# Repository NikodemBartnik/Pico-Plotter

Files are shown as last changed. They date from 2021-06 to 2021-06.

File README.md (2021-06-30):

# Pico Plotter
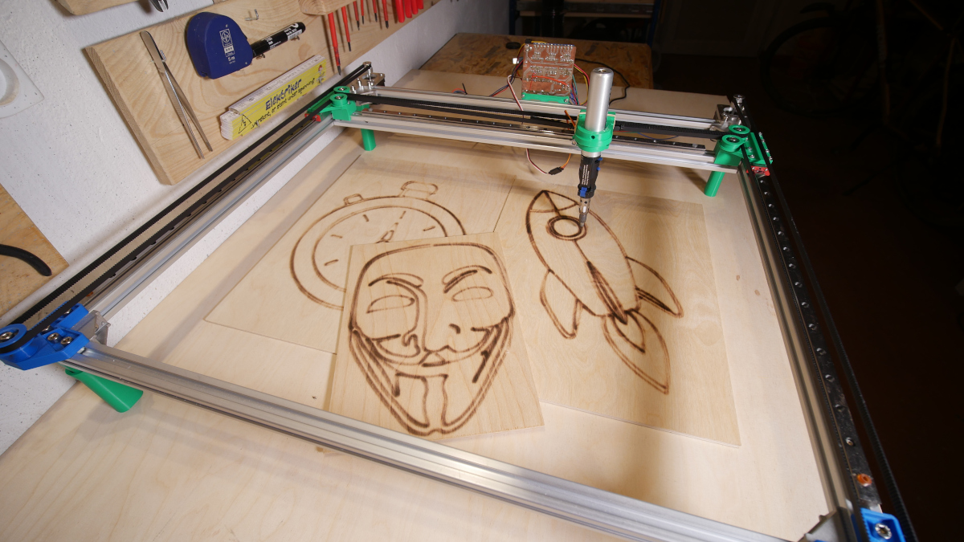
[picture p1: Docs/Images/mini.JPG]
Pico Plotter image

3D printed Raspberry Pi Pico H-Bot plotter programmed in MicroPython capable of drawing on paper and burning wood with versatip.

## Description

Main purpose of this project was to practice Python programing, design something cool and understand basics of how CNC machines, Gcode senders etc. works. This project is probably a great starting point to learn about basics of any CNC machine, as it is very simple and code is very minimal. 3D printed parts are optimized for support less printing (most of them but not all) and can be printed out of PLA. 
## Parts
#### Electronics
| Name | Amount | Link 1 | Link 2 | Link 3 |
| --- | --- | --- | --- | --- |
| Motors | 2 | [https://bit.ly/3jrCJqY](https://bit.ly/3jrCJqY) | [https://bit.ly/3w9vsim](https://bit.ly/3w9vsim) | [https://amzn.to/3jlCU7o](https://amzn.to/3jlCU7o) |
| Stepper drivers | 2 | [https://bit.ly/3608XSl](https://bit.ly/3608XSl) | [https://bit.ly/3Abaz9P](https://bit.ly/3Abaz9P) | [https://amzn.to/3yjyXV9](https://amzn.to/3yjyXV9) |
| Power supply | 1 | [https://bit.ly/3qzeEjz](https://bit.ly/3qzeEjz) | [https://bit.ly/3qzJbxF](https://bit.ly/3qzJbxF) | [https://amzn.to/2T9NVOx](https://amzn.to/2T9NVOx) |
| Raspberry Pi Pico | 1 | [https://bit.ly/2US6Spl](https://bit.ly/2US6Spl) | [https://bit.ly/3Aegafp](https://bit.ly/3Aegafp) | [https://amzn.to/2Tjz9Vd](https://amzn.to/2Tjz9Vd) |
| USB to UART converter | 1 | [https://bit.ly/3vZQIqF](https://bit.ly/3vZQIqF) | [https://bit.ly/36488Il](https://bit.ly/36488Il) | [https://amzn.to/3dsafcT](https://amzn.to/3dsafcT) |
| Micro servo | 1 | [https://bit.ly/3A8MjoF](https://bit.ly/3A8MjoF) | [https://bit.ly/3jrOihS](https://bit.ly/3jrOihS) | [https://amzn.to/367zPQh](https://amzn.to/367zPQh) |
| Small components | \- | | |
#### Mechanics
| Name | Amount | Link 1 | Link 2 | Link 3 |
| --- | --- | --- | --- | --- |
| Aluminium profile 2020 600mm | 5 | [https://bit.ly/2UF2auT](https://bit.ly/2UF2auT) | [https://bit.ly/3hjPS2F](https://bit.ly/3hjPS2F) | [https://amzn.to/2UcRjs5](https://amzn.to/2UcRjs5) |
| MGN12 Linear rail 500mm | 3 | [https://bit.ly/3qwWoHM](https://bit.ly/3qwWoHM) | [https://bit.ly/3jvdd4f](https://bit.ly/3jvdd4f) | [https://amzn.to/3Adcs5K](https://amzn.to/3Adcs5K) |
| MGN12H linear block | 5 | [https://bit.ly/3qyKxsE](https://bit.ly/3qyKxsE) | [https://bit.ly/3AkVN0r](https://bit.ly/3AkVN0r) | [https://amzn.to/3h266yv](https://amzn.to/3h266yv) |
| GT2 Pulley | 2 | [https://bit.ly/3y7doGW](https://bit.ly/3y7doGW) | [https://bit.ly/3AbJDXp](https://bit.ly/3AbJDXp) | [https://amzn.to/3h2xc8I](https://amzn.to/3h2xc8I) |
| GT2 Belt | 5m | [https://bit.ly/3h44CUH](https://bit.ly/3h44CUH) | [https://bit.ly/2U5sbDr](https://bit.ly/2U5sbDr) | [https://amzn.to/3x8Wgk0](https://amzn.to/3x8Wgk0) |
| 625ZZ Bearing | 6 | [https://bit.ly/2USf3Sz](https://bit.ly/2USf3Sz) | [https://bit.ly/2TbLKKo](https://bit.ly/2TbLKKo) | [https://amzn.to/3vZVZyt](https://amzn.to/3vZVZyt) |
| Corner connectors | 4 | [https://bit.ly/3h1PA1G](https://bit.ly/3h1PA1G) | [https://bit.ly/3qLDTj3](https://bit.ly/3qLDTj3) | [https://amzn.to/2Ua83Af](https://amzn.to/2Ua83Af) |
| Screws, T nuts etc. | | | |
#### Tools
| Name | Link 1 | Link 2 | Link 3 |
| --- | --- | --- | --- |
| 3D printer | [https://bit.ly/3qxoAu7](https://bit.ly/3qxoAu7) | [https://bit.ly/3xZZaHU](https://bit.ly/3xZZaHU) | [https://amzn.to/3y25gHV](https://amzn.to/3y25gHV) |
| CNC Machine | [https://indystry.cc/indymill/](https://indystry.cc/indymill/) | [https://indystry.cc/dremel-cnc/](https://indystry.cc/dremel-cnc/) | |
| Gas soldering iron | [https://amzn.to/3jEaGoH](https://amzn.to/3jEaGoH) | [https://bit.ly/3dqgHBm](https://bit.ly/3dqgHBm) |
## Getting Started
You don't need any special libraries or additional files, assuming you have Python installed you have everything you need.
In order to upload script to Raspberry Pi Pico I used [Thonny](https://thonny.org/)

### Executing program
Before executing the Gcode sender change port of your raspberry pi pico and also path to the file that you want to print
To execute Gcode sender script simply change directory to where the file is located and type in the terminal:
```
python GcodeSender.py
```

## Help

If you need help, see the problem or want to contribute open an issue.

## Author
[Nikodem Bartnik](https://nikodembartnik.pl/)

## License

This project is licensed under the MIT license.

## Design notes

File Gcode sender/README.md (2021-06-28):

Very simple command line based Gcode sender. Not really useful for bigger projects, but great to understand how such things work, experiment and control the Pico Plotter.

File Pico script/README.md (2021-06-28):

MicroPython script for Raspberry Pi Pico for a pico plotter

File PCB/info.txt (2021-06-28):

Here are links to libraries I used for this PCB:
https://github.com/Lobo-T/RPI-Pico-Eagle-lib

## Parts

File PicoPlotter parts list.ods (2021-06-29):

Electronics
Name | Amount | Link 1 | Link 2 | Link 3 | Comments
Motors | 2 | https://bit.ly/3jrCJqY | https://bit.ly/3w9vsim | https://amzn.to/3jlCU7o
Stepper drivers | 2 | https://bit.ly/3608XSl | https://bit.ly/3Abaz9P | https://amzn.to/3yjyXV9
Power supply | 1 | https://bit.ly/3qzeEjz | https://bit.ly/3qzJbxF | https://amzn.to/2T9NVOx | 12V 3A
Raspberry Pi Pico | 1 | https://bit.ly/2US6Spl | https://bit.ly/3Aegafp | https://amzn.to/2Tjz9Vd
USB to UART converter | 1 | https://bit.ly/3vZQIqF | https://bit.ly/36488Il | https://amzn.to/3dsafcT
Micro servo | 1 | https://bit.ly/3A8MjoF | https://bit.ly/3jrOihS | https://amzn.to/367zPQh
Small components | - |  |  |  | Pin headers, LEDs
Mechanics
Name | Amount | Link 1 | Link 2 | Link 3 | Comments
Aluminium profile 2020 600mm | 5 | https://bit.ly/2UF2auT | https://bit.ly/3hjPS2F | https://amzn.to/2UcRjs5
MGN12 Linear rail 500mm | 3 | https://bit.ly/3qwWoHM | https://bit.ly/3jvdd4f | https://amzn.to/3Adcs5K | Usually one liner block is included in each rail so you may need to buy only 2 additional blocks
MGN12H linear block | 5 | https://bit.ly/3qyKxsE | https://bit.ly/3AkVN0r | https://amzn.to/3h266yv
GT2 Pulley | 2 | https://bit.ly/3y7doGW | https://bit.ly/3AbJDXp | https://amzn.to/3h2xc8I
GT2 Belt | 5m | https://bit.ly/3h44CUH | https://bit.ly/2U5sbDr | https://amzn.to/3x8Wgk0
625ZZ Bearing | 6 | https://bit.ly/2USf3Sz | https://bit.ly/2TbLKKo | https://amzn.to/3vZVZyt
Corner connectors | 4 | https://bit.ly/3h1PA1G | https://bit.ly/3qLDTj3 | https://amzn.to/2Ua83Af
Screws, T nuts etc.
Tools
Name | Amount | Link 1 | Link 2 | Link 3 | Comments
3D printer |  | https://bit.ly/3qxoAu7 | https://bit.ly/3xZZaHU | https://amzn.to/3y25gHV
CNC Machine |  | https://indystry.cc/indymill/ | https://indystry.cc/dremel-cnc/
Gas soldering iron |  | https://amzn.to/3jEaGoH | https://bit.ly/3dqgHBm |  | I am using the versatip from Dremel, never tested the other one

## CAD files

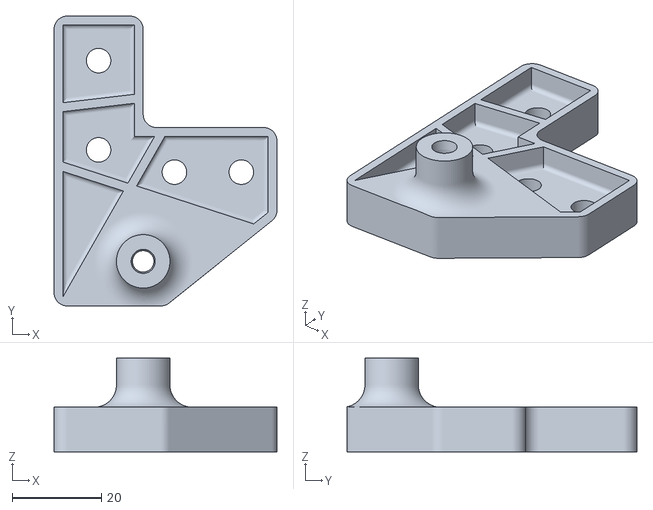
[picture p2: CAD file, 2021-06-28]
3D printed/Bearing holder left.stl
50.0 x 65.0 x 21.0

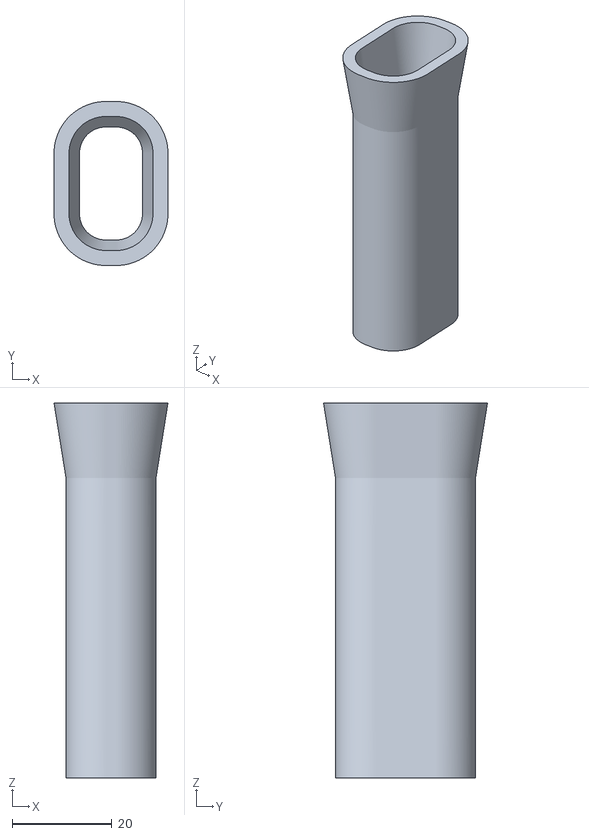
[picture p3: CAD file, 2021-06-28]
3D printed/Leg extension.stl
22.8 x 32.8 x 75.0

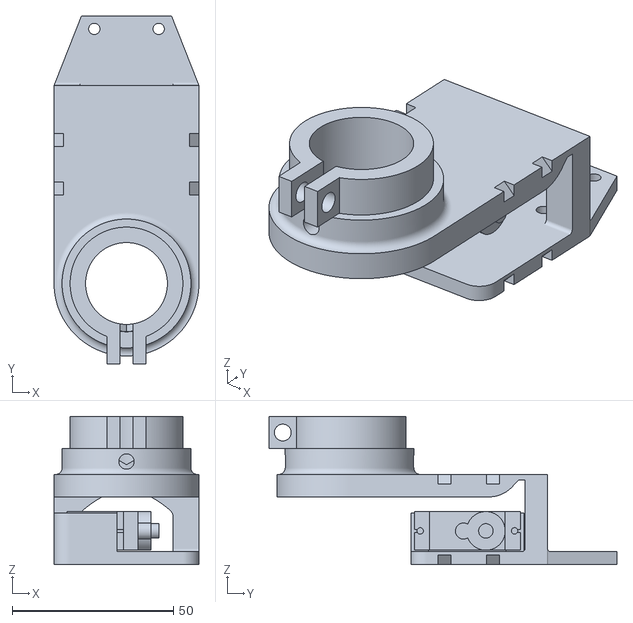
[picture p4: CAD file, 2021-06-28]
3D printed/X carriage.stl
45.0 x 108.1 x 46.0

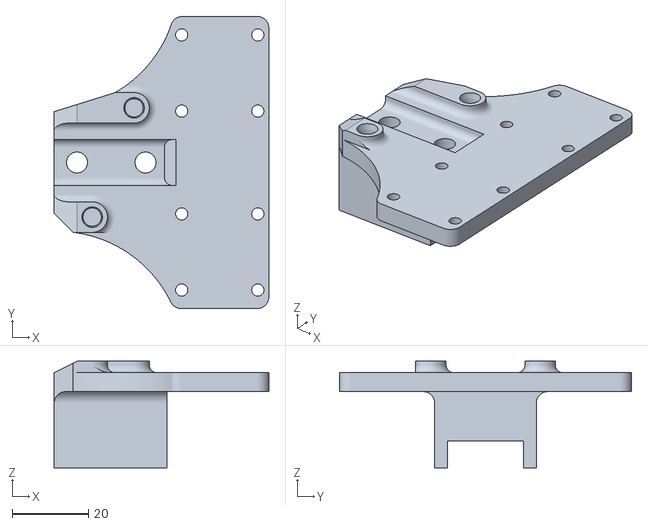
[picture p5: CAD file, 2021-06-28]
3D printed/Y right.stl
56.4 x 76.7 x 28.0

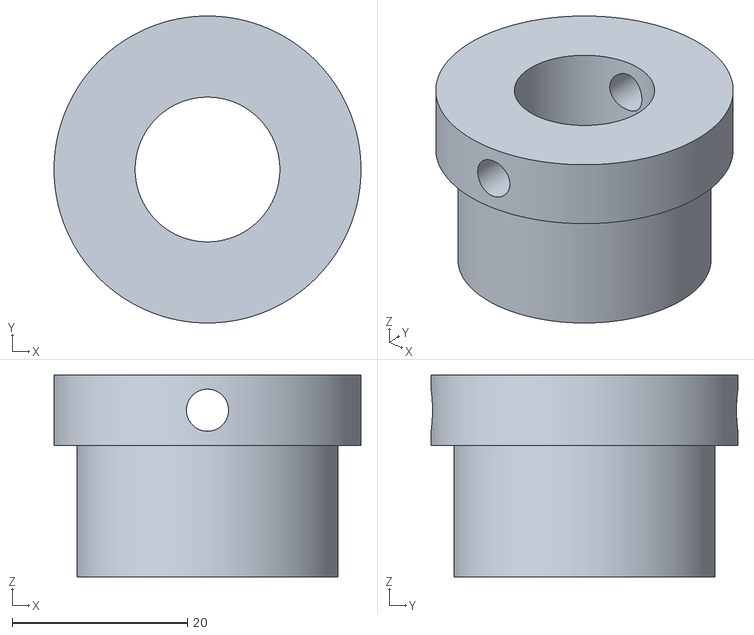
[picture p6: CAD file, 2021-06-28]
3D printed/Pen holder.stl
35.0 x 35.0 x 23.0

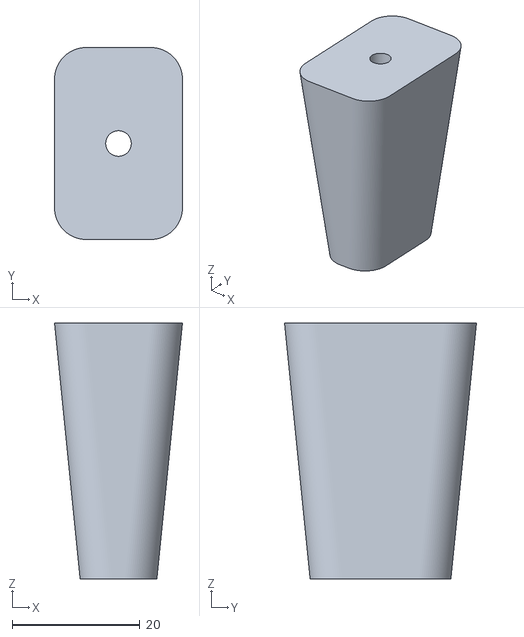
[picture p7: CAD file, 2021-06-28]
3D printed/Leg.stl
20.0 x 30.0 x 40.0

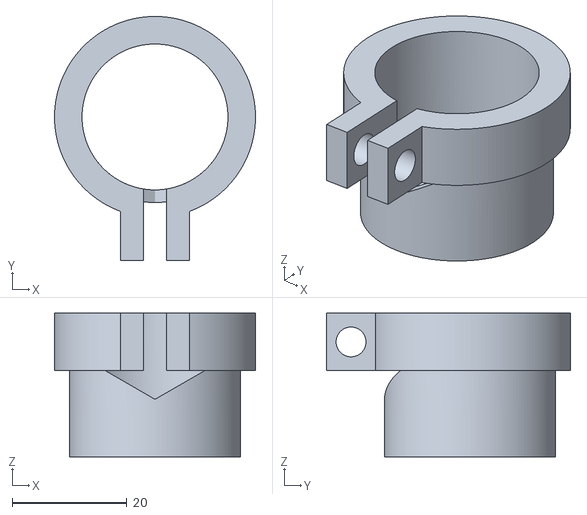
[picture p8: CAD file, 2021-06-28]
3D printed/Verastip holder.stl
35.0 x 42.5 x 25.0

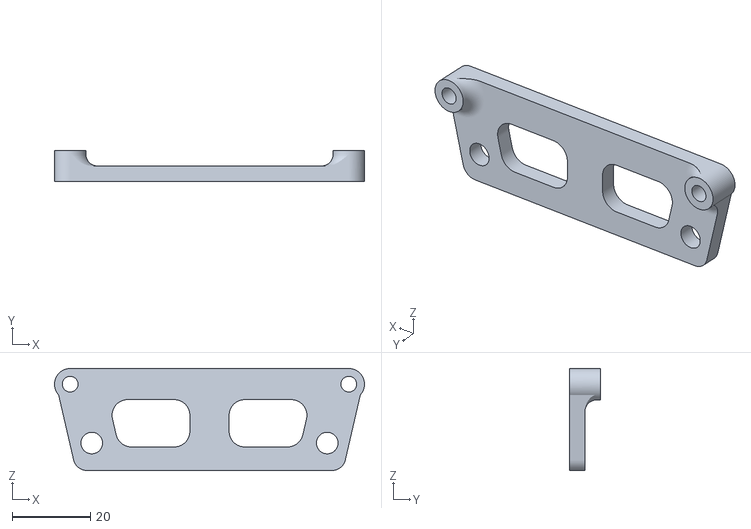
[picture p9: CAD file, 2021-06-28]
3D printed/PCB holder.stl
79.0 x 8.00 x 26.0

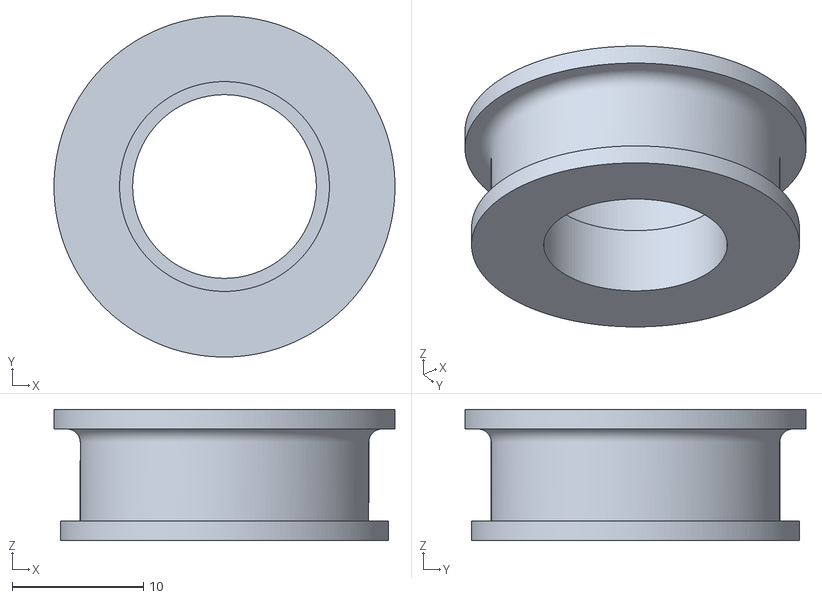
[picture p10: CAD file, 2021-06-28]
3D printed/pulley.stl
26.0 x 26.0 x 10.0

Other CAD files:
3D printed/Bearing holder right.stl
3D printed/Y left.stl
PicoPlotter.f3z

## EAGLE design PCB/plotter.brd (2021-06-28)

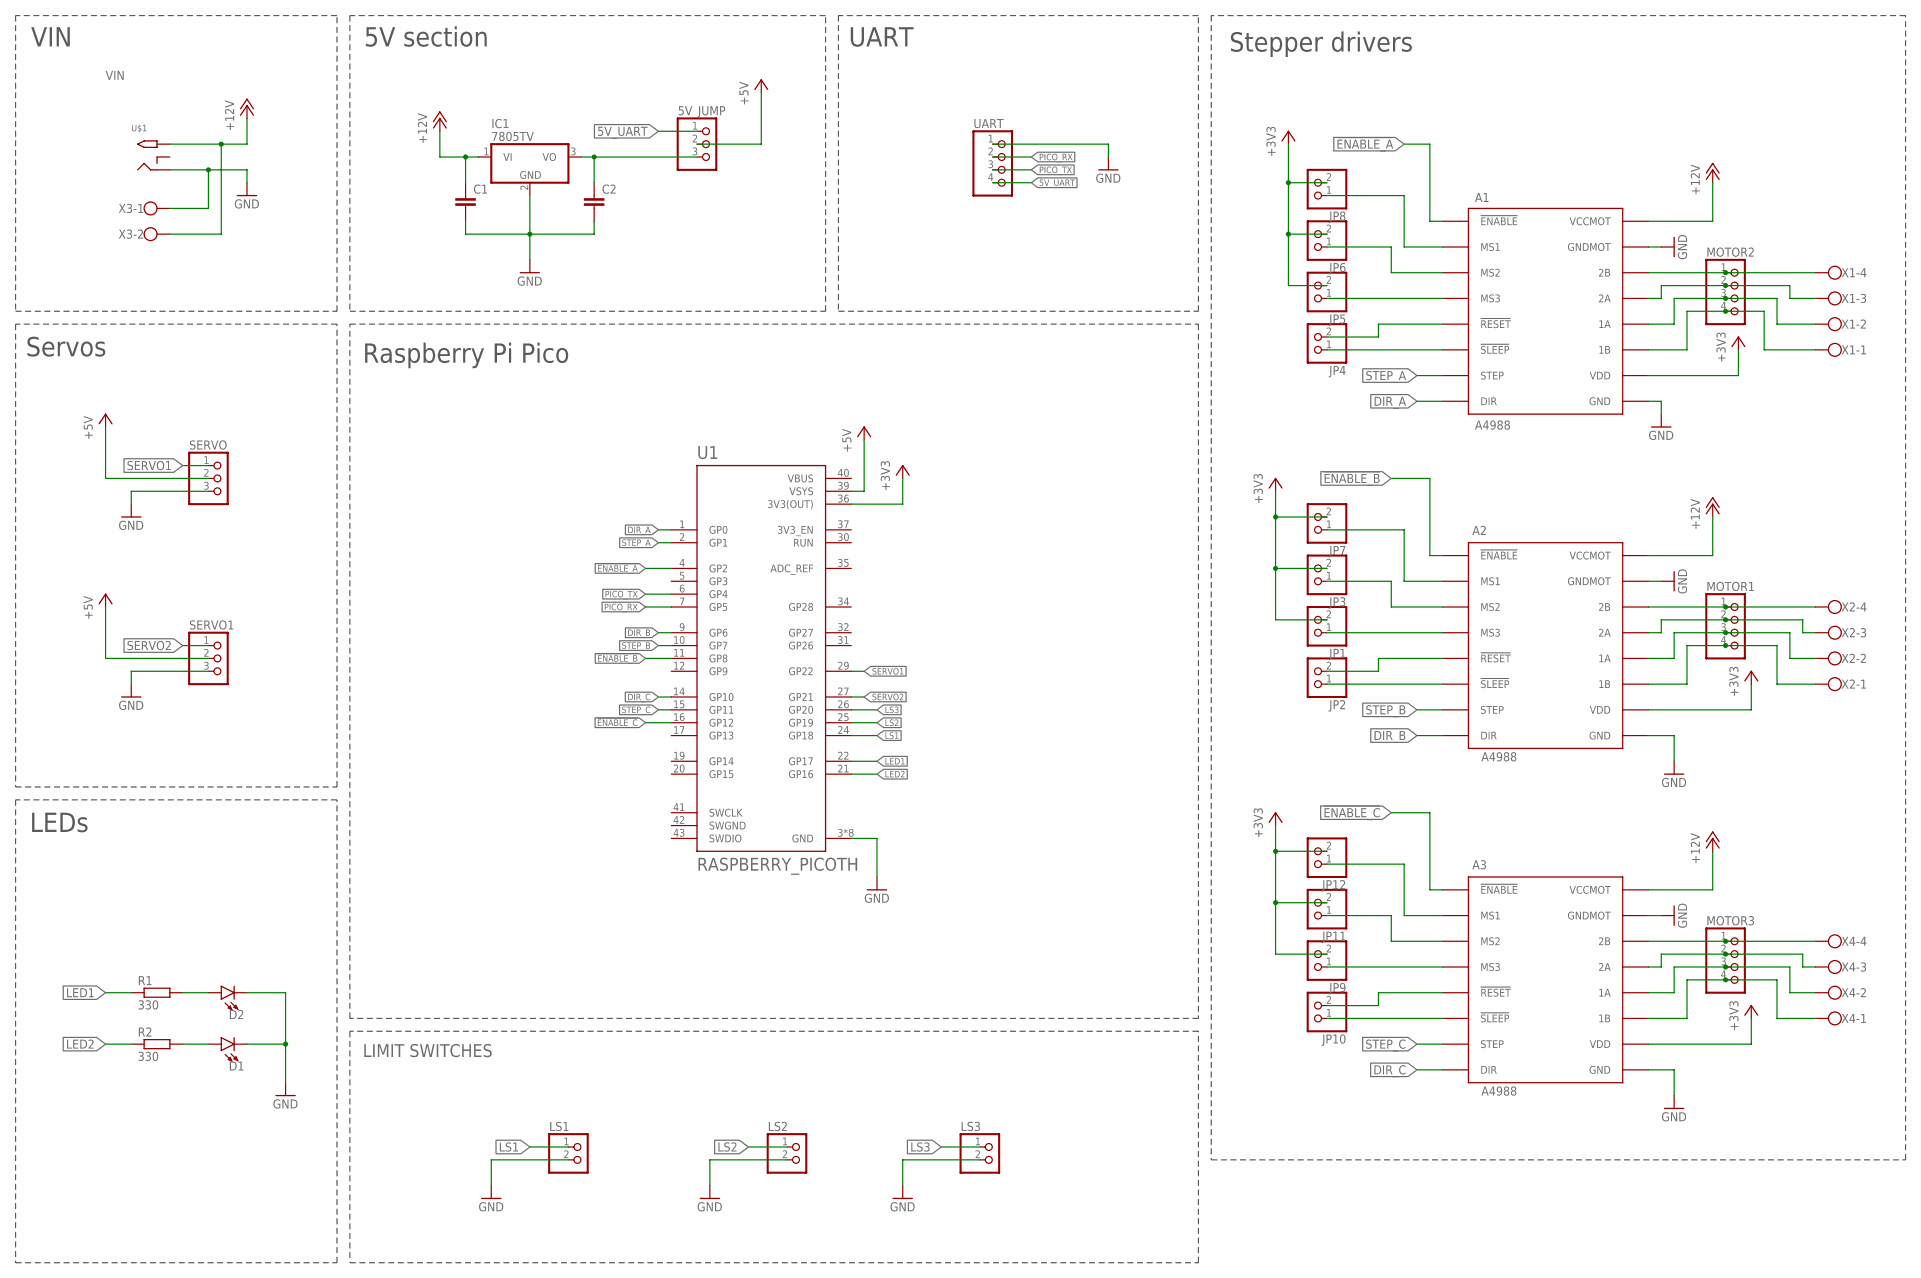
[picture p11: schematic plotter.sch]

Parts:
5V_JUMP: PINHD-1X3; 1X03
A1, A2, A3: A4988
C1, C2: C-EUC0805; C0805
D1, D2: LED5MM; LED_5MM
IC1: 7805TV; TO220V
JP1, JP2, JP3, JP4, JP5, JP6, JP7, JP8, JP9, JP10, JP11, JP12: PINHD-1X2; 1X02
LS1, LS2, LS3: PINHD-1X2; 1X02
MOTOR1, MOTOR2, MOTOR3: PINHD-1X4; 1X04
R1, R2: 330; R0805
SERVO, SERVO1: PINHD-1X3; 1X03
U1: RASPBERRY_PICOTH; PICO-PKG-TH
U$1: 2.1MMJACKTHM; PJ-102A
UART: PINHD-1X4; 1X04
X1, X2, X4: W237-4
X3: W237-102

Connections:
5V_UART: 5V_JUMP.1, UART.4
!ENABLE_A: A1.!ENABLE, U1.4 (GP2)
!ENABLE_B: A2.!ENABLE, U1.11 (GP8)
!ENABLE_C: A3.!ENABLE, U1.16 (GP12)
+3V3: A1.VDD, A2.VDD, A3.VDD, JP1.2, JP3.2, JP5.2, JP6.2, JP7.2, JP8.2, JP9.2, JP11.2, JP12.2, U1.36 (3V3(OUT))
+5V: 5V_JUMP.2, SERVO.2, SERVO1.2, U1.39 (VSYS)
+12V: A1.VCCMOT, A2.VCCMOT, A3.VCCMOT, C1.1, IC1.1 (VI), U$1.TIP, X3.2
DIR_A: A1.DIR, U1.1 (GP0)
DIR_B: A2.DIR, U1.9 (GP6)
DIR_C: A3.DIR, U1.14 (GP10)
GND: A1.GND, A1.GNDMOT, A2.GND, A2.GNDMOT, A3.GND, A3.GNDMOT, C1.2, C2.2, D1.K (C), D2.K (C), IC1.2 (GND), LS1.2, LS2.2, LS3.2, SERVO.3, SERVO1.3, U1.3 (GND), U1.8 (GND), U1.13 (GND), U1.18 (GND), U1.23 (GND), U1.28 (GND), U1.33 (GND), U1.38 (GND), U$1.RING, UART.1, X3.1
LED1: R1.1, U1.22 (GP17)
LED2: R2.1, U1.21 (GP16)
LS1: LS1.1, U1.24 (GP18)
LS2: LS2.1, U1.25 (GP19)
LS3: LS3.1, U1.26 (GP20)
unnamed: A1.2B, MOTOR2.1, X1.4
unnamed: A1.2A, MOTOR2.2, X1.3
unnamed: A1.1A, MOTOR2.3, X1.2
unnamed: A1.1B, MOTOR2.4, X1.1
unnamed: A2.2B, MOTOR1.1, X2.4
unnamed: A2.2A, MOTOR1.2, X2.3
unnamed: A2.1A, MOTOR1.3, X2.2
unnamed: A2.1B, MOTOR1.4, X2.1
unnamed: 5V_JUMP.3, C2.1, IC1.3 (VO)
unnamed: D2.A, R1.2
unnamed: D1.A, R2.2
unnamed: A2.!SLEEP, JP2.1
unnamed: A2.!RESET, JP2.2
unnamed: A2.MS3, JP1.1
unnamed: A2.MS2, JP3.1
unnamed: A2.MS1, JP7.1
unnamed: A1.!SLEEP, JP4.1
unnamed: A1.!RESET, JP4.2
unnamed: A1.MS3, JP5.1
unnamed: A1.MS2, JP6.1
unnamed: A1.MS1, JP8.1
unnamed: A3.2B, MOTOR3.1, X4.4
unnamed: A3.2A, MOTOR3.2, X4.3
unnamed: A3.1A, MOTOR3.3, X4.2
unnamed: A3.1B, MOTOR3.4, X4.1
unnamed: A3.!SLEEP, JP10.1
unnamed: A3.!RESET, JP10.2
unnamed: A3.MS3, JP9.1
unnamed: A3.MS2, JP11.1
unnamed: A3.MS1, JP12.1
PICO_RX: U1.7 (GP5), UART.2
PICO_TX: U1.6 (GP4), UART.3
SERVO1: SERVO.1, U1.29 (GP22)
SERVO2: SERVO1.1, U1.27 (GP21)
STEP_A: A1.STEP, U1.2 (GP1)
STEP_B: A2.STEP, U1.10 (GP7)
STEP_C: A3.STEP, U1.15 (GP11)
SWGND: U1.42 (SWGND)
VBUS: U1.40 (VBUS)

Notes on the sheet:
VIN
LIMIT SWITCHES
LEDs
Servos
5V section
UART
Stepper drivers
Raspberry Pi Pico

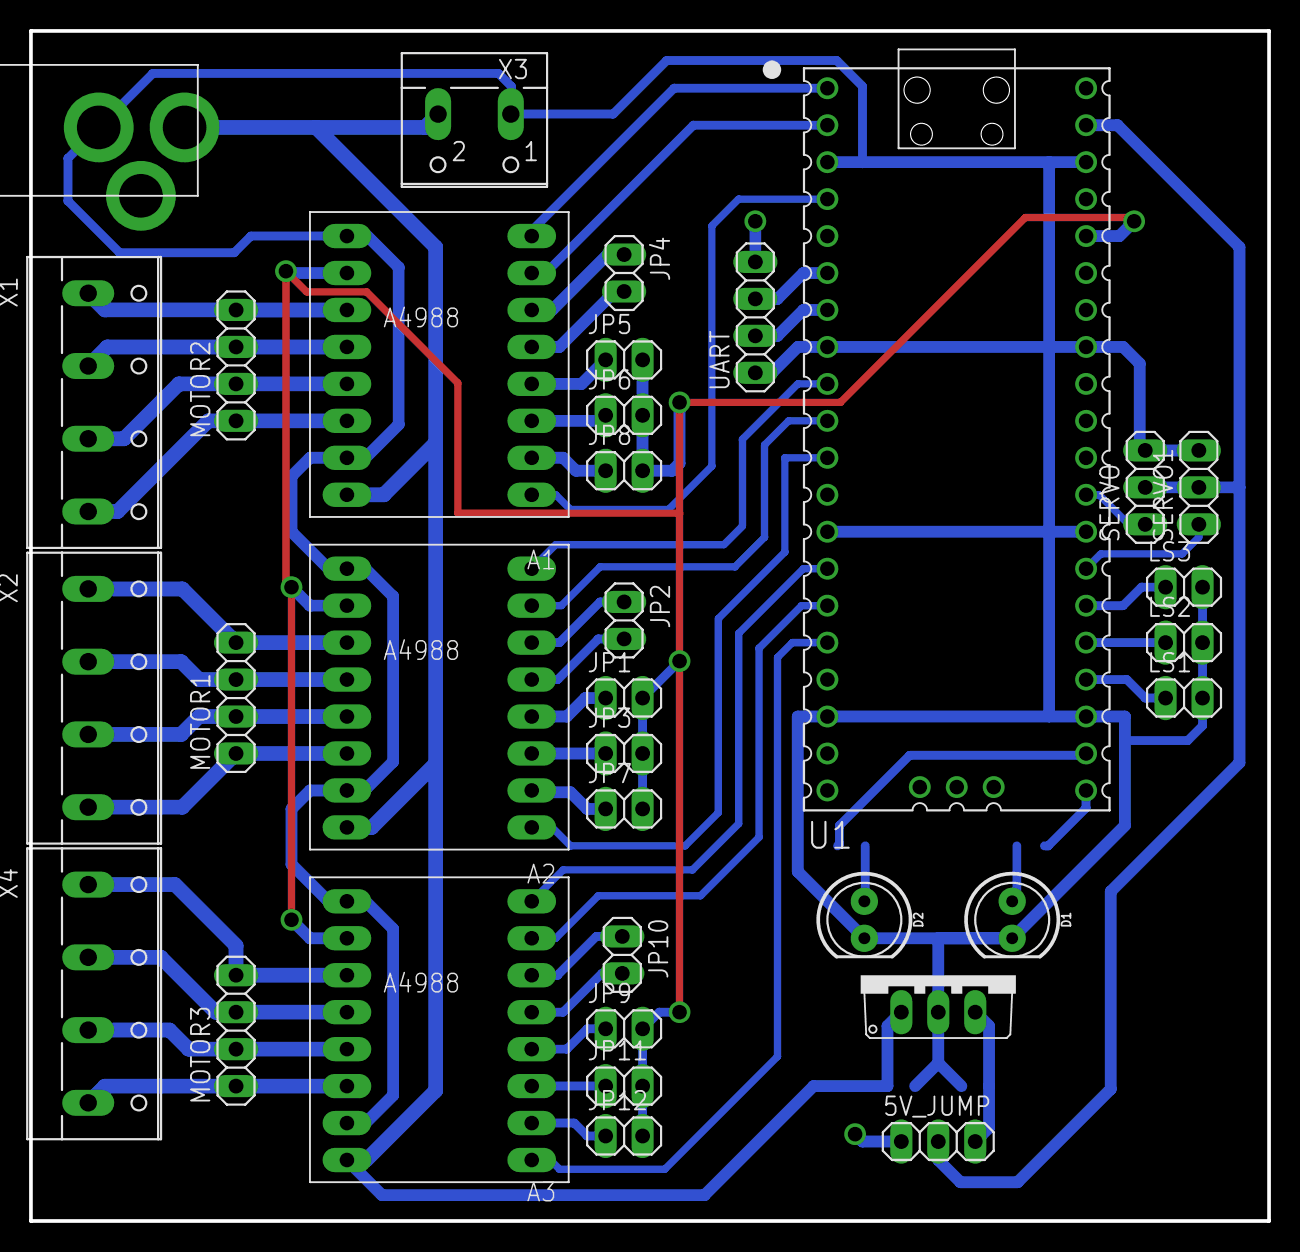
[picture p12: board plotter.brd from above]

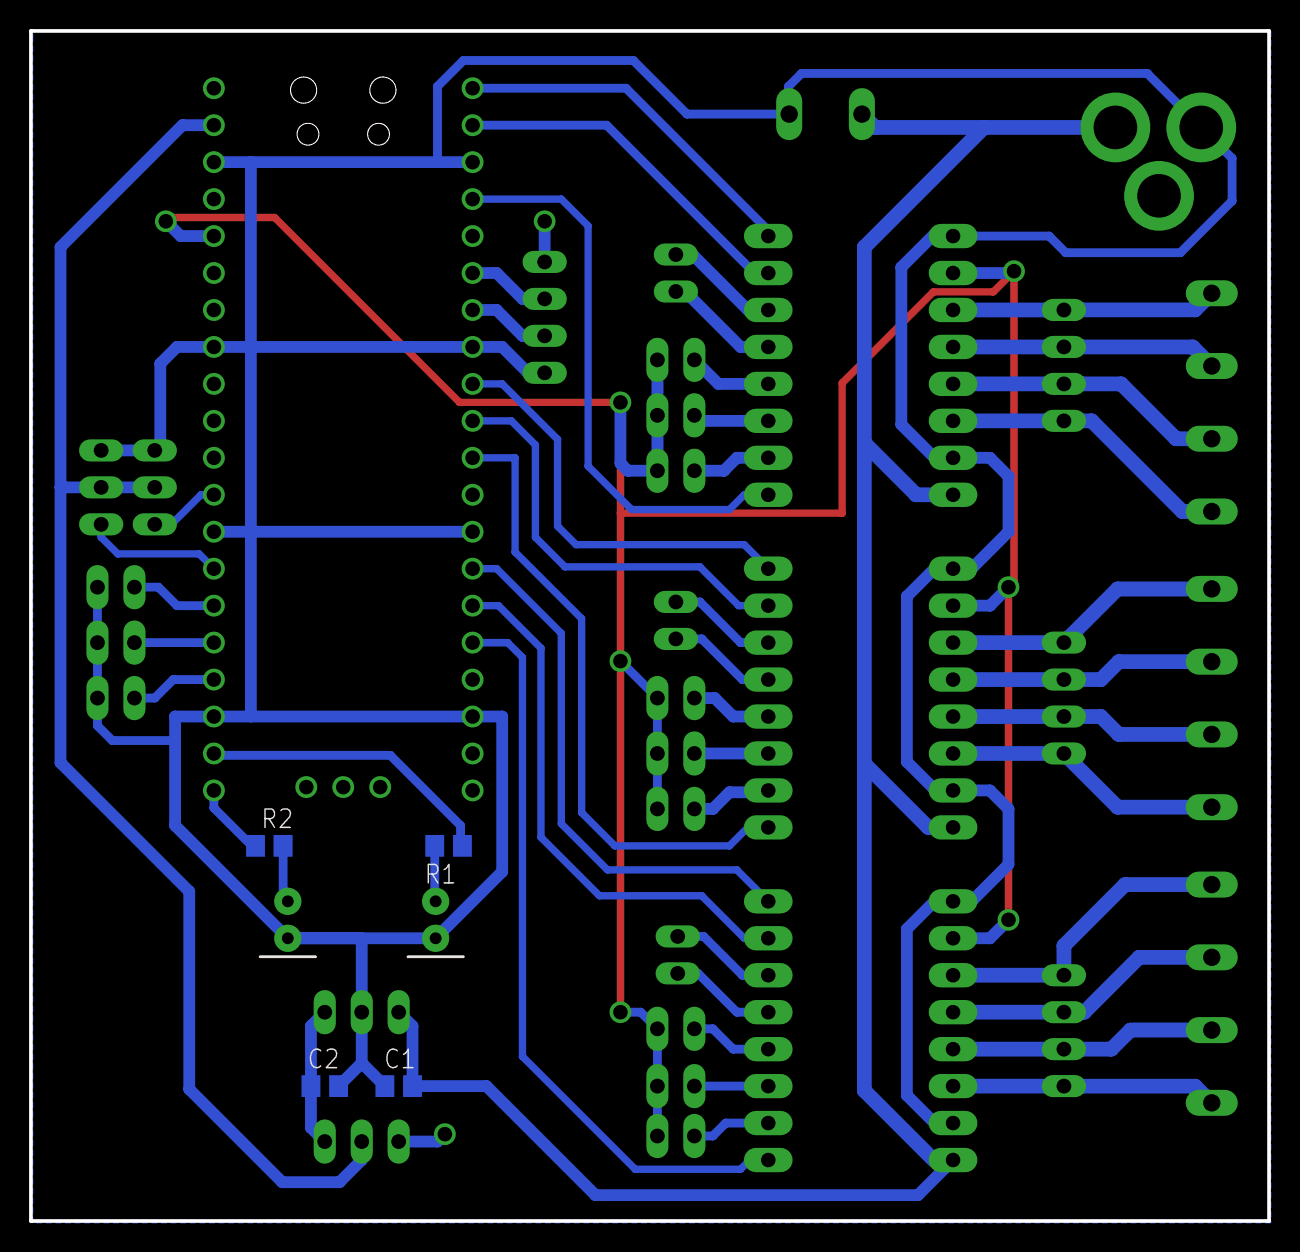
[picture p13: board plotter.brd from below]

Board: 2 copper layers, 85.1 x 81.8 mm, 38 parts (4 on the bottom side), 53 nets.

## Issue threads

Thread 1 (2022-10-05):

TypeError: object with buffer protocol required on widows

erleto74, 2022-10-05:
Hello,
I have an error when trying to testing this project. Can you help me how to solve this problem?
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
I test it in win 10 with thonny ver 4.0.0

NikodemBartnik, 2022-10-05:
You should run this code on Pi Pico, not your windows machine

erleto74, 2022-10-05:
Thank you, I waw

Closed 2022-10-05.

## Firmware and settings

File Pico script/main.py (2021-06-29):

import utime
from machine import Pin, UART, PWM
uart = machine.UART(1, 115200)

#constants
STEPSPERMM = 80
MMPERSTEP = 1/STEPSPERMM
DIR_A = 0
STEP_A = 1
nENABLE_A = 2
STEP_DELAY = 20

DIR_B = 6
STEP_B = 7
nENABLE_B = 8

DIR_C = 10
STEP_C = 11
nENABLE_C = 12

SERVO_PIN = 21

x_step_pos = 0
y_step_pos = 0


dir_A = Pin(DIR_A, Pin.OUT)
step_A = Pin(STEP_A, Pin.OUT)
nenable_A = Pin(nENABLE_A, Pin. OUT)

dir_B = Pin(DIR_B, Pin.OUT)
step_B = Pin(STEP_B, Pin.OUT)
nenable_B = Pin(nENABLE_B, Pin. OUT)

servo = None

def EnableMotors():
    nenable_A.value(0)
    nenable_B.value(0)
    

def DisableMotors():
    nenable_A.value(1)
    nenable_B.value(1)
    

#a = 0 move A, a = 1 move B
def OneStep(a, direction):
    if a == 0:
        dir_A.value(direction)
        step_A.value(0)
        step_A.value(1)
    elif a == 1:
        dir_B.value(direction)
        step_B.value(0)
        step_B.value(1)
        
    

#To move to (X, Y) we need to calculate dA = dX + dY and dB = dX - dY
def MoveToPosition(x, y):
    global x_step_pos
    global y_step_pos
    #x and y steps to do, different than a and b steps to do
    x = x/MMPERSTEP
    y = y/MMPERSTEP
    x_steps_to_do = round(x) - x_step_pos
    y_steps_to_do = round(y) - y_step_pos
    a_steps_to_do = x_steps_to_do + y_steps_to_do
    b_steps_to_do = x_steps_to_do - y_steps_to_do
    x_step_pos = x
    y_step_pos = y
    
    #deciding on which way the motors should spin
    directionA = 0 if a_steps_to_do > 0 else 1
    directionB = 0 if b_steps_to_do > 0 else 1
    
    #after obatining the direction we can convert to absolute values for simplicity
    a_steps_to_do = abs(a_steps_to_do)
    b_steps_to_do = abs(b_steps_to_do)

    #here we will store the error for the axis with sliced movement
    if a_steps_to_do == b_steps_to_do:
        for i in range(a_steps_to_do):
            OneStep(0, directionA)
            OneStep(1, directionB)
            StepsDelay()
        
    else:
        sliced_axis_error = 0
        sliced_axis_increment = b_steps_to_do/a_steps_to_do if a_steps_to_do > b_steps_to_do else a_steps_to_do/b_steps_to_do
        
        if a_steps_to_do > b_steps_to_do:
            for i in range(a_steps_to_do):
                OneStep(0, directionA)
                sliced_axis_error += sliced_axis_increment
                if sliced_axis_error >= 1:
                    OneStep(1, directionB)
                    sliced_axis_error -= 1
                StepsDelay()
            
        elif a_steps_to_do < b_steps_to_do:
            for i in range(b_steps_to_do):
                OneStep(1, directionB)
                sliced_axis_error += sliced_axis_increment
                if sliced_axis_error >= 1:
                    OneStep(0, directionA)
                    sliced_axis_error -= 1
                StepsDelay()
    
    
    
def StepsDelay():
    utime.sleep_us(STEP_DELAY)
    
    
def UartRead():
    return uart.readline()


def UartSendOK():
    uart.write('OK\n')
    

def ProcessGcode(inputLine):
    UartSendOK()
    #dictionary with variables to return
    toReturn = {}
    inputLine = inputLine.strip('\n\r')
    inputLine = inputLine.split(';', 1)[0]
    print(inputLine)
    if len(inputLine) > 0:
        gcode = inputLine.split(' ')
        for command in gcode:
            if command[0] == 'X':
                #do things with X
                toReturn['X'] = command[1:]
            elif command[0] == 'Y':
                #do things with Y
                toReturn['Y'] = command[1:]
            elif command[0] == 'Z':
                #do things with Z
                toReturn['Z'] = command[1:]
            elif command[0] == 'F':
                #do things with F
                toReturn['F'] = command[1:]
            elif command[0] == 'G':
                #do things with G
                toReturn['G'] = command[1:]
    return toReturn


def ExecuteGcode(commands):
    global x_step_pos
    global y_step_pos
    global STEP_DELAY
    if 'F' in commands:        
        STEP_DELAY = int(5000 - 5*int(commands['F']))
        if STEP_DELAY < 20: STEP_DELAY = 20
        print("New step delay: " + str(STEP_DELAY))
    if 'Z' in commands:
        ServoWrite(0 if float(commands['Z']) > 0.1 else 30)
    if 'X' in commands or 'Y' in commands:
        MoveToPosition(float(commands['X']) if 'X' in commands else x_step_pos*MMPERSTEP, float(commands['Y']) if 'Y' in commands else y_step_pos*MMPERSTEP)
    if 'G' in commands:
        if(commands['G'] == '28'):
            x_step_pos = 0
            y_step_pos = 0
    
                
def ServoWrite(angle):
    servo.duty_ns(int((angle/180)*1000000+700000))
    utime.sleep_ms(100)


def ServoInit():
    global servo
    servo = PWM(Pin(21))
    servo.freq(50)
    servo.duty_ns(700000)
    
    
EnableMotors()
ServoInit()
while(1):
    ExecuteGcode(ProcessGcode(str(UartRead(), "utf-8")))

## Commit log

2021-06-28 Added Gcode sender script and MicroPython code for Raspberry Pi Pico
2021-06-29 Updated readme and parts list
    [PicoPlotter parts list.ods]

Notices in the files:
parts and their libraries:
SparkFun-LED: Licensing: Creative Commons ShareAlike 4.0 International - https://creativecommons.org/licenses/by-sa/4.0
